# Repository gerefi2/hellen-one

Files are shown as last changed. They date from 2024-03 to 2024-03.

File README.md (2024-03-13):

# TL,DR: 

hellen-one is a toolset to produce custom PCBs by merging gerber files of known proven functional modules into trivial _frame_ PCB with mostly just the main vehicle connector.

* fork https://github.com/gerefi/hellen-example/ repo to get github actions and meta files
* make sure github actions are enabled/enable github actions on your fork
* replace xxx and yyy in ``revision.txt`` with name of your board
* create youboard.kicad_pcb from [proven modules](https://github.com/gerefi2/hellen-one/tree/master/modules) using KiCAD 6 or 7
* push into github to trigger hellen-one gerber expert and gerber merge (that's where the hellen magic happens! for instance gerber export is taken care by [export.sh](https://github.com/gerefi2/hellen-one/blob/master/kicad/bin/export.sh) script which github action would invoke _automatically_. Just watch for the yellow circle to turn into a green checkmark.)
* (sorry rotation only by factor of 90 degrees at this point)
* order your using fabrication files from 'boards' folder!

Please see how some of the open source boards are done and follow the pattern:

## Open Source Boards

* https://github.com/gerefi/alphax-4chan
* https://github.com/gerefi/uaefi
* https://github.com/gerefi/alphax-2chan
* https://github.com/gerefi/hellen154hyundai
* https://github.com/gerefi/hellen121vag
* https://github.com/gerefi/hellen88bmw
* https://github.com/gerefi2/hellen81/

This repository contains all scripts and data to create Hellen One boards for [gerefi](https://github.com/gerefi/gerefi)!

See also https://github.com/gerefi/gerefi/wiki/Hellen-One-Platform

Hellen One is a DIY PnP ECU board construction toolset.

Do you have a car with a rare or non-standard ECU connector pinout?
Do you want a custom DIY ECU but don't want to design it from scratch?

Then Hellen One is for you!

Please see Hellen One Wiki for more info:

https://github.com/gerefi2/hellen-one/wiki

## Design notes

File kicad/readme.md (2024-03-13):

# Some of the modules were designed in KiCAD

If you are designing a new ECU frame see https://github.com/gerefi2/hellen-one/tree/master/modules

doThis folder contains module _source_ files, not reusable resulting frames like [here](../modules).

See https://github.com/gerefi2/hellen-one/wiki/scripts-howto#how-to-create-a-module

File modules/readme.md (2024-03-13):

This folder contains KiCAD footprints/gerbers/PDFs which hellen-one framework would merge into your frame design.

See https://github.com/gerefi2/hellen-one/wiki for module documentation

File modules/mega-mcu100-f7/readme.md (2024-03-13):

For instance 
* [https://jlcpcb.com/partdetail/Stmicroelectronics-STM32F765VGT6/C435845](STM32F765VGT6)
* STM32F777VIT6
* STM32F767VIT6
* STM32F765VIT6

Full list see https://github.com/gerefi2/hellen-one/issues/341

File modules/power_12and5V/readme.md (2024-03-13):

See https://github.com/gerefi2/hellen-one/wiki/module-power12-and-5

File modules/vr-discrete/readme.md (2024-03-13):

See https://github.com/gerefi2/hellen-one/wiki/module-vr-discrete

[Source files](../../kicad/modules/hellen1-vr-discrete)

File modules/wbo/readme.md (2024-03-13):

[Source files](../../kicad/modules/hellen1-wbo)

## Changelog

0.4:
  - two side assembly
  - BUG: CANH/CANL traces are flipped

0.3: 
  - MOSFET through-hole option 
  - https://github.com/gerefi2/hellen-one/blob/master/modules/wbo/wbo-0.3-migration.png remove one track and refill zones
     
0.3 v2:
  - 1mm vias under MOSFET for hand soldering

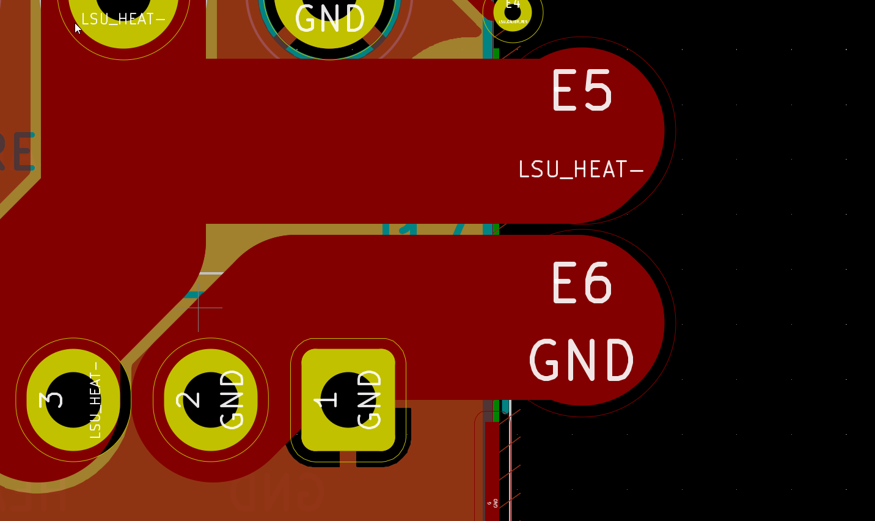
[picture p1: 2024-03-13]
modules/wbo/wbo-0.3-migration.png

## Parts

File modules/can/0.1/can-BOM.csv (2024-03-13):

Comment | Designator | Footprint | LCSC Part #
100n | C430, C431 | C0603 | C14663
PESD1CAN | D430 | SOT-23 | C343993
Hellen One : CAN Module interface | M430
120 | R430 | R0603 | C22787
TJA1051T/3/1J | U430 | SO8 | C38695

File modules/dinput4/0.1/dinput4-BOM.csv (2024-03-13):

Comment | Designator | Footprint | LCSC Part #
1n | C490, C491, C492, C493 | C0603 | C1588
Module:dinput4/0.1 | M490
680k | R490 | R0603-4 | C145776
10k | R491 | R0603-4 | C29718
74HC2G17GW | U490, U491 | SOT-363 | C94189

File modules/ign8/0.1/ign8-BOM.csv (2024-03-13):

Comment | Designator | Footprint | LCSC Part #
100n | C460, C461 | C0603 | C14663
Module:ign8/0.1 | M460
10 | R461, R462, R463, R464, R466, R467, R468, R469 | R0603 | C22859
SN74LVC4245APWR | U460 | TSSOP24 | C7859

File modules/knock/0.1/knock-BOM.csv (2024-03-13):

Comment | Designator | Footprint | LCSC Part #
100n | C470 | C0603 | C14663
3.3n | C471 | C0603 | C1613
330p | C472 | C0603 | C1664
47p | C473 | C0603 | C1671
680p | C474 | C0603 | C1630
Module:knock/0.1 | M470
470k | R470 | R0603 | C23178
100k | R471, R473 | R0603 | C25803
12k | R472 | R0603 | C22790
33k | R474 | R0603 | C4216
LMV321IDBVR | U470, U471 | SOT23-5 | C7972

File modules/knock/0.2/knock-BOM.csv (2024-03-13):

Comment | Designator | Footprint | LCSC Part #
100n | C470 | C0402 | C307331
3.3n | C471 | C0402 | C26404
330p | C472 | C0402 | C13533
47p | C473 | C0402 | C1567
680p | C474 | C0603 | C1630
Module:knock/0.2 | M470
470k | R470 | R0402 | C25790
100k | R471, R473 | R0402 | C25741
12k | R472 | R0402 | C25752
33k | R474 | R0402 | C25779
LMV321IDBVR | U470, U471 | SOT23-5 | C7972

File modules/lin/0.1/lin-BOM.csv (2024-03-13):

Comment | Designator | Footprint | LCSC Part #
100n | C440 | C0603 | C14663
B5819W | D440, D441 | SOD-123 | C8598
Hellen One : LIN Module interface | M440
1k | R440 | R0603 | C21190
TJA1021T/20/CM | U440 | SO8 | C128810

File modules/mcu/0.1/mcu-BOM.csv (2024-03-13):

Comment | Designator | Footprint | LCSC Part #
100n | C101, C105, C106, C107, C108, C109, C110, C111, C112, C113, C117, C118, C119, C120, C121, C122, C123, C124, C125, C126, C127, C128, C129, C130, C135, C139 | C0603 | C14663
4.7u | C102, C103, C104, C137, C138, C140 | C0603 | C19666
2.2u | C114, C131 | C0603 | C23630
12p | C115, C116 | C0603 | C38523
18p | C132, C136 | C0603 | C1647
B5819W | D101, D107 | SOD-123 | C8598
SRV05-4-P-T7 | D102 | SOT23-6 | C85364
LED-RED-0603 | D103 | LED-0603 | C2286
LED-GREEN-0603 | D104 | LED-0603 | C72043
LED-BLUE-0603 | D105 | LED-0603 | C72041
LED-YELLOW-0603 | D106 | LED-0603 | C72038
SDFL2012Q3R3KTF | L101 | L0805 | C51725
Module:mcu/0.1 | M101
4.7k | R101, R107, R108, R109, R110, R111, R112, R113, R115, R117, R118, R125, R126 | R0603-4 | C66697
10k | R102, R103, R105, R121, R122, R123, R127, R128 | R0603 | C25804
100 | R104, R106 | R0603 | C22775
47 | R114 | R0603 | C23182
510 | R116, R119, R120, R124 | R0603 | C23193
10k | R129, R130 | R0603-4 | C29718
0 | R131 | R0402 | C17168
AMS1117-3.3 | U101 | SOT-223 | C6186
LMV324IPWR | U102, U104, U106, U107, U108, U109 | TSSOP14 | C398929
AP2337SA-7 | U103 | SOT-23 | C150497
STM32F427IGT6 | U105 | LQFP176 | C117817
XC6206P332MR | U111 | SOT-23 | C5446
32.768 kHz | Y101 | SMD2012 | C99009
8.0 MHz | Y102 | SMD5032 | C115962

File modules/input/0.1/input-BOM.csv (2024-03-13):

Comment | Designator | Footprint | LCSC Part #
1n | C200, C202, C203, C216, C217, C218, C219 | C0603 | C1588
10n | C201, C208, C209, C210, C211 | C0603 | C57112
100n | C204, C205, C206, C207, C212, C213, C214, C215, C220, C221, C222, C223, C224, C225, C226 | C0603 | C14663
2.2u | C227, C228, C229 | C0805 | C49217
SRV05-4-P-T7 | D200, D201, D202, D203, D204, D205 | SOT23-6 | C85364
P6SMB6.8CA | D206 | SMB | C78395
Module:input/0.1 | M200
4.7k | R200, R201, R202, R203, R204, R205, R207 | R0603-4 | C1980
680k | R206, R209, R211 | R0603-4 | C145776
10k | R208, R210 | R0603-4 | C29718
510 | R212, R213, R214, R215 | R0603 | C23193
3.3k | R216 | R0603 | C22978

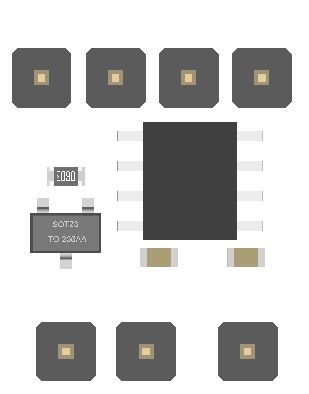
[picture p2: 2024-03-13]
tests/boards.EXAMPLE/hellen1test-a/board/misc/hellen1test-a-components.png

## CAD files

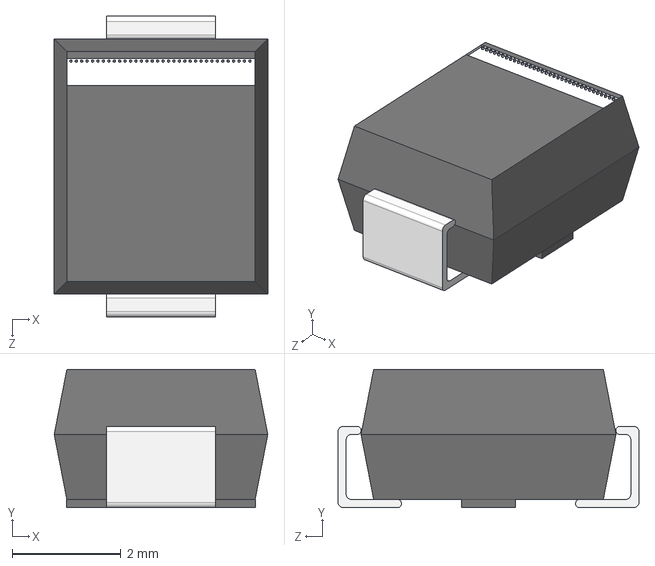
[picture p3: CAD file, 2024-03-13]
kicad/models/DO-214AA(SMB).STEP
3.94 x 2.55 x 5.55 mm

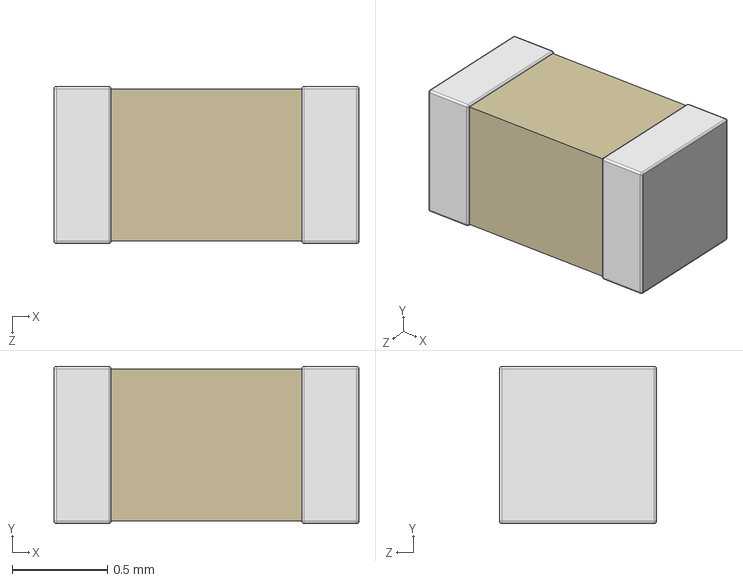
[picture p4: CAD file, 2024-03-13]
kicad/models/0603 cap.STEP
1.60 x 0.824 x 0.824 mm

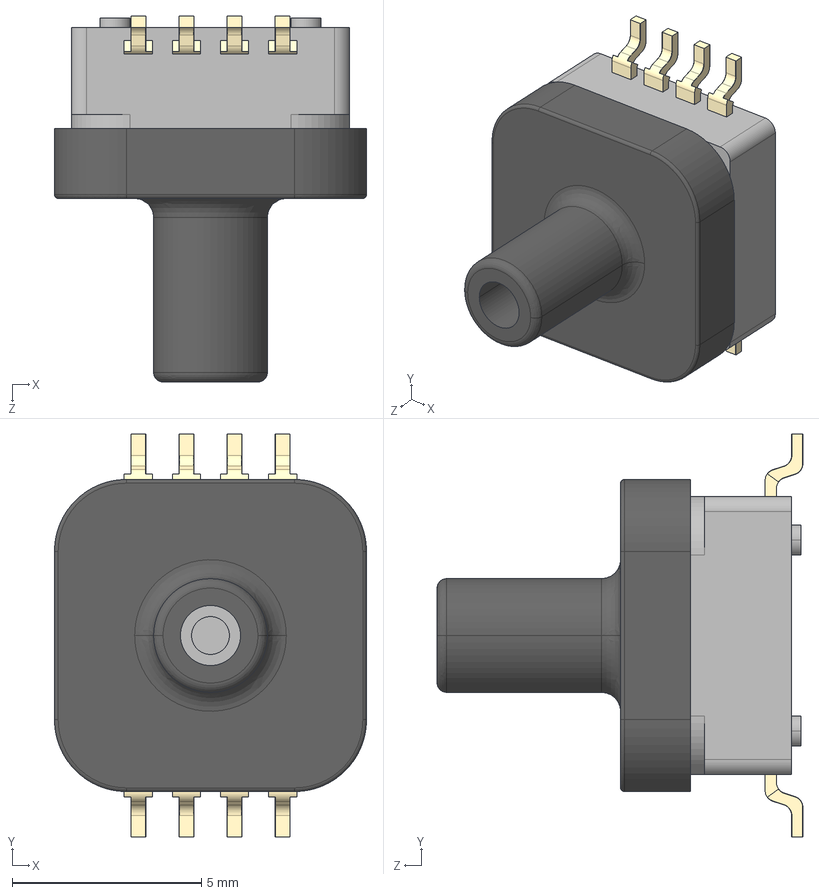
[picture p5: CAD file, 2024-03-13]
kicad/models/MPXH6400A.STEP
8.25 x 10.7 x 9.67 mm
User Library-ZlozenieMPXH6400A_Komin
User Library-ZlozenieMPXH6400A_podstawa
User Library-ZlozenieMPXH6400A_NOGA x 8

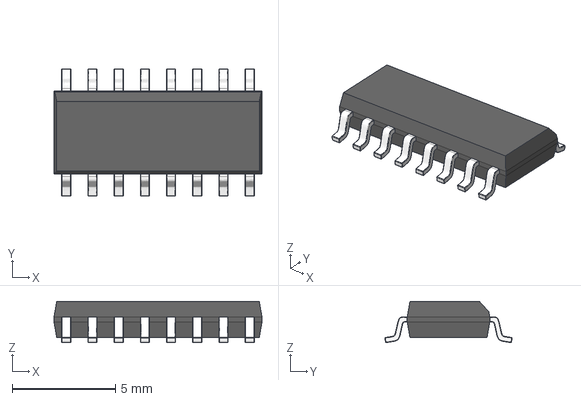
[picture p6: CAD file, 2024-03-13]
kicad/models/SOIC16 narrow.STEP
10.1 x 6.16 x 2.00 mm

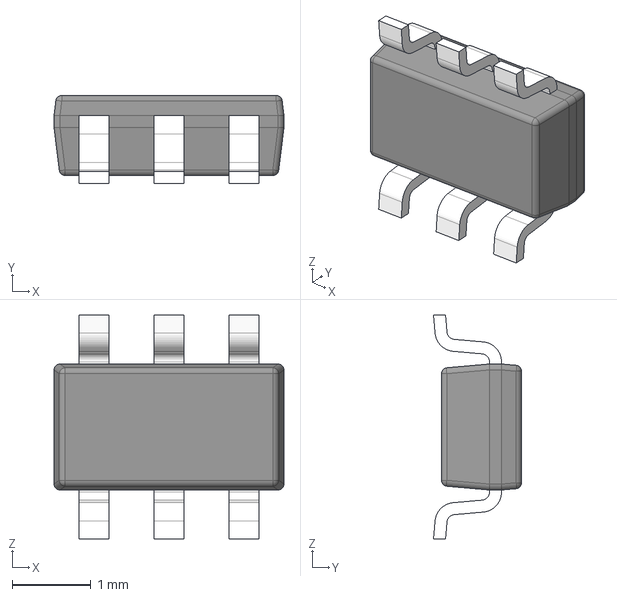
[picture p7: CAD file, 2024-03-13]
kicad/models/sot-23-6.stp
2.92 x 1.12 x 2.84 mm
BODY_MF06A
LEAD_MF06A x 6

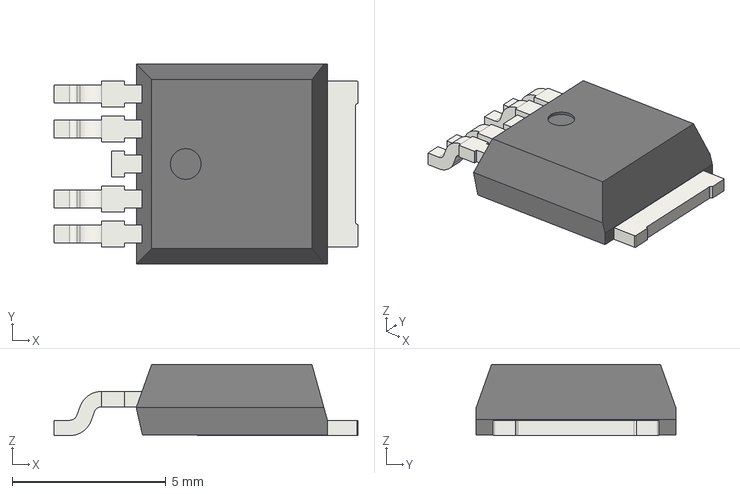
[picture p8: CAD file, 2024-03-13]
kicad/models/DPAK-5.STEP
9.90 x 6.50 x 2.32 mm

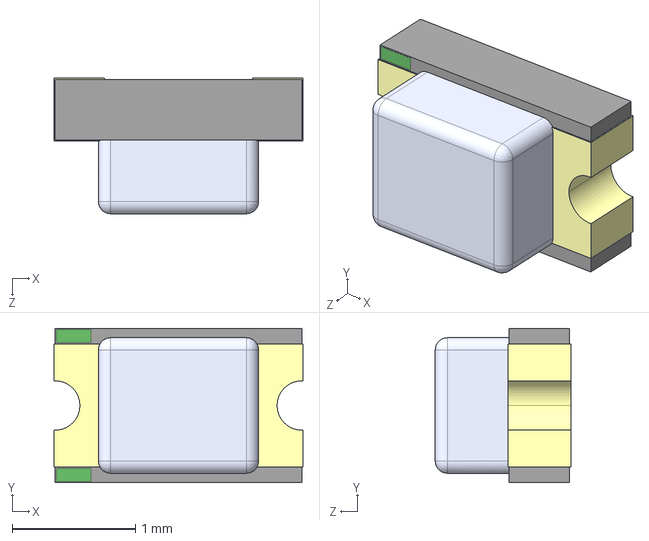
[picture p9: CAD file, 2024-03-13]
kicad/models/LED0805-YELLOW.STEP
2.02 x 1.25 x 1.10 mm

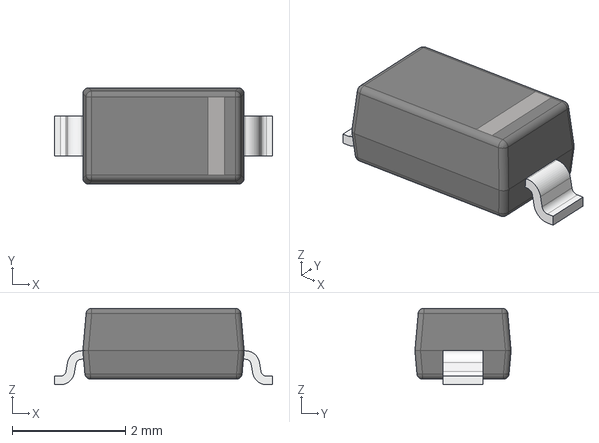
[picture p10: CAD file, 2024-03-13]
kicad/models/DO-215AD.stp
3.85 x 1.70 x 1.35 mm

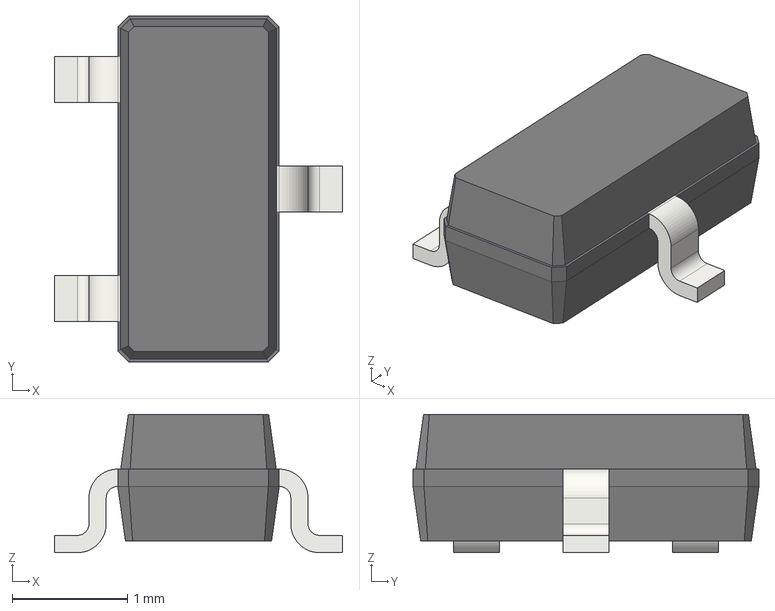
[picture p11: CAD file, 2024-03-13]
kicad/models/SOT-23.STEP
2.50 x 3.00 x 1.20 mm

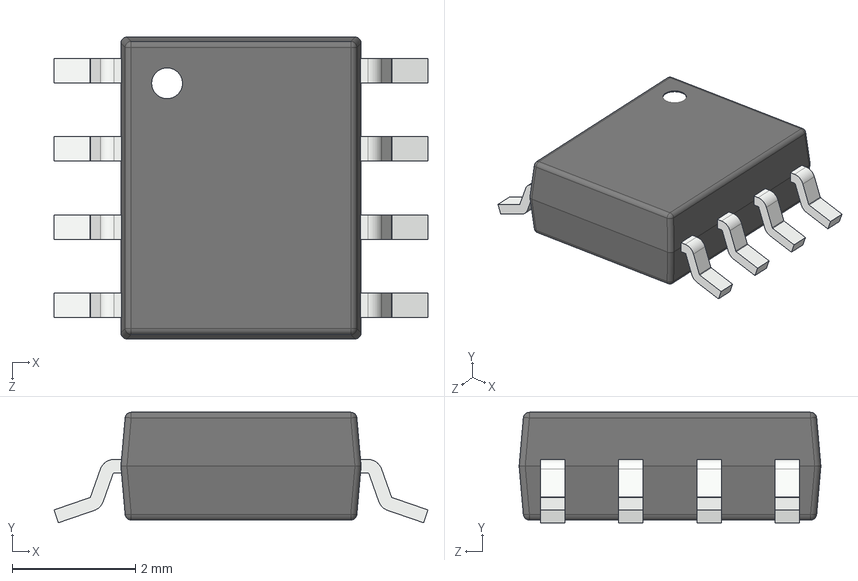
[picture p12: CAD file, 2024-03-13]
kicad/models/PG-DSO-8.STEP
6.07 x 1.79 x 4.90 mm

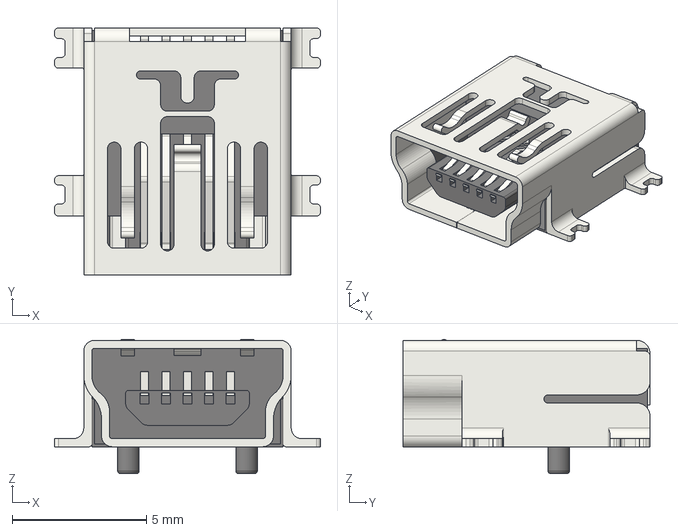
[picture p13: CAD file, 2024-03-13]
kicad/models/USB-Mini-B-Horizontal.STEP
9.90 x 9.20 x 5.00 mm

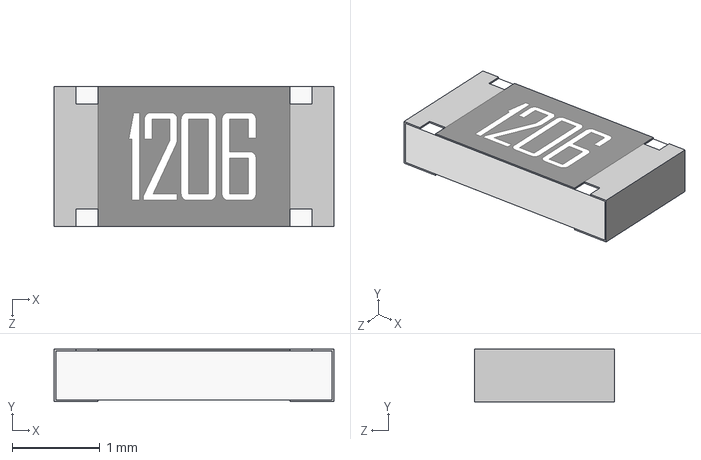
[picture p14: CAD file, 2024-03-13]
kicad/models/1206 resistor.STEP
3.20 x 0.6 x 1.60 mm

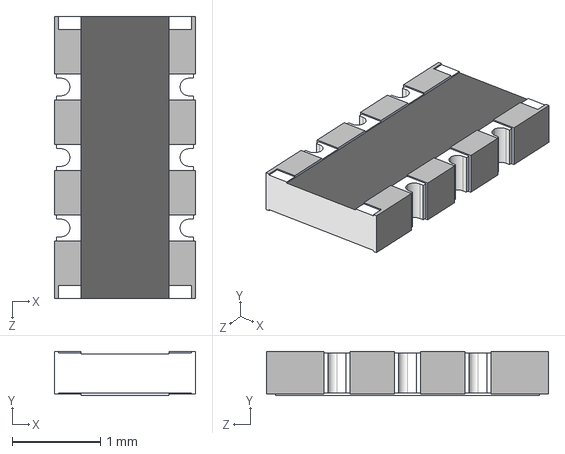
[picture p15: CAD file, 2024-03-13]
kicad/models/CAY16-F4.STEP
1.60 x 0.5 x 3.20 mm

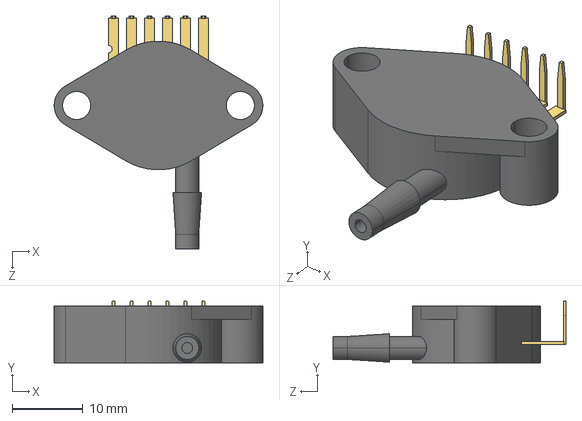
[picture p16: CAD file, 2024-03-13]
kicad/models/MPX4250AP.STEP
29.5 x 8.72 x 32.9 mm

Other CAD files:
kicad/models/SOD323F.STEP
kicad/models/SOIC08 narrow.STEP
kicad/models/USB-B-Vertical.step
kicad/models/DPAK.STEP
kicad/models/0402 resistor.STEP
kicad/models/0603 resistor.STEP
kicad/models/0805 cap.STEP
kicad/models/0805 resistor.STEP
kicad/models/LGA-12-2x2x0_9.STEP
kicad/models/PinHeader_1x06_P2.54mm_Vertical.STEP
kicad/models/PinHeader_1x08_P2.54mm_Vertical.STEP
kicad/models/PinHeader_2x05_P1.27mm_Vertical_SMD.STEP
kicad/models/PowerSO20.STEP
kicad/models/SKRKAHE020.STEP
kicad/models/SOD123F.STEP
kicad/models/SOT-223.STEP
kicad/models/SOT-363.STEP
kicad/models/TSSOP14.STEP

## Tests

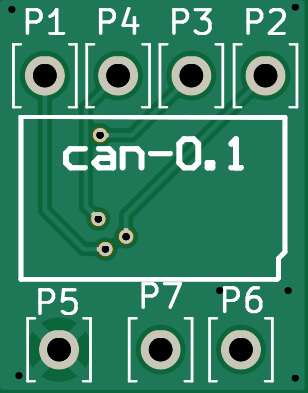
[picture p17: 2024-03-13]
tests/boards.EXAMPLE/hellen1test-a/board/misc/hellen1test-a-bottom.png

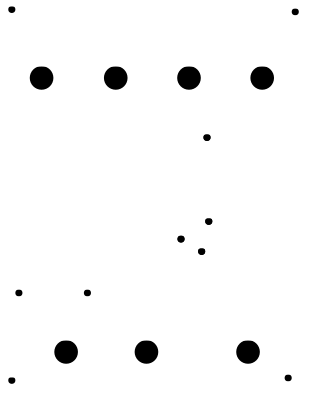
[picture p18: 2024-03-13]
tests/boards.EXAMPLE/hellen1test-a/board/misc/hellen1test-a-outline.png

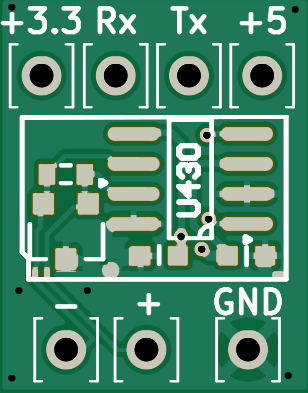
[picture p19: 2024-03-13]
tests/boards.EXAMPLE/hellen1test-a/board/misc/hellen1test-a-top.png

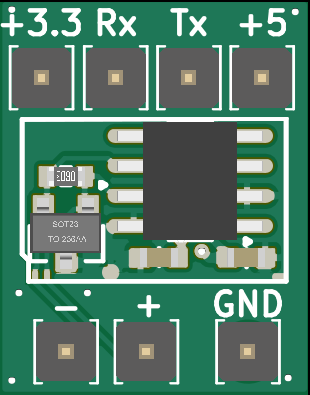
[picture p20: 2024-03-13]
tests/boards.EXAMPLE/hellen1test-a/board/hellen1test-a.png

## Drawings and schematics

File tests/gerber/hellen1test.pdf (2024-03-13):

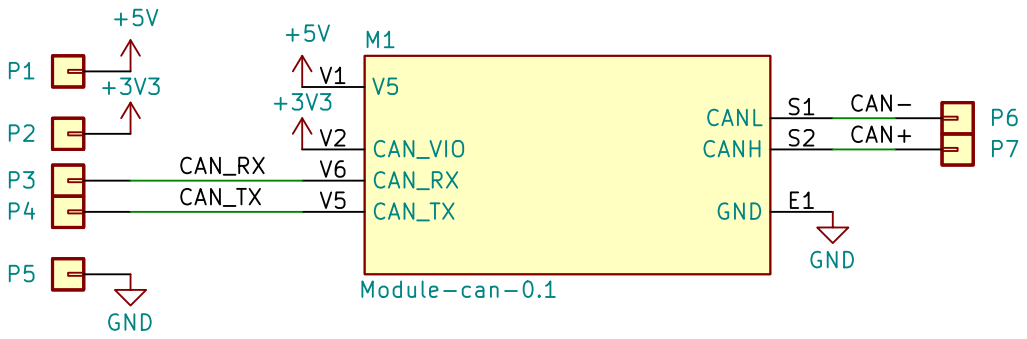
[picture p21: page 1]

File: hellen1test.kicad_sch Sheet: /
Id: 1/1 Title: Hellen-One Test Board

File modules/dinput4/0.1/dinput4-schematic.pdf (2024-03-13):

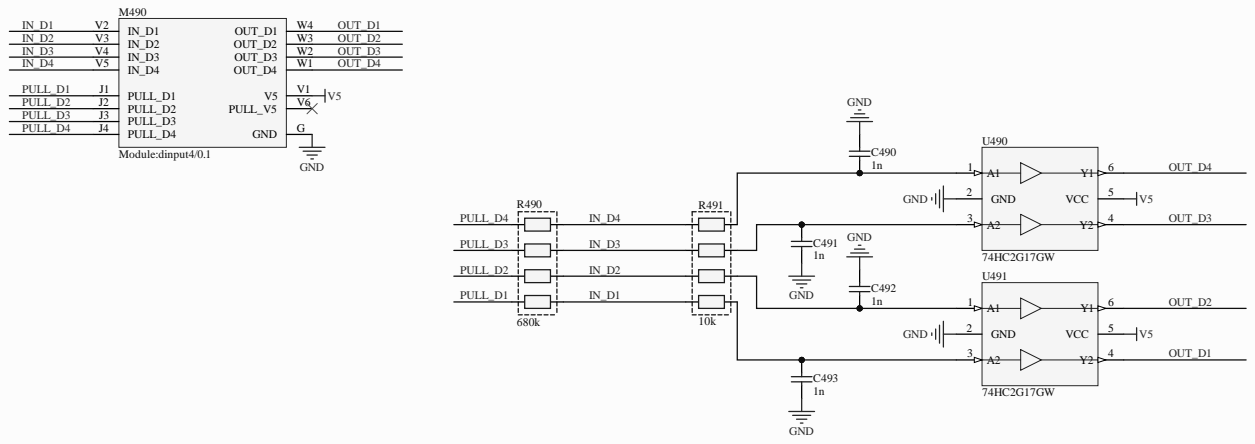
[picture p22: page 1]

Hellen-One VR andreika

rusEFI EMS https://rusefi.co
Hellen-One

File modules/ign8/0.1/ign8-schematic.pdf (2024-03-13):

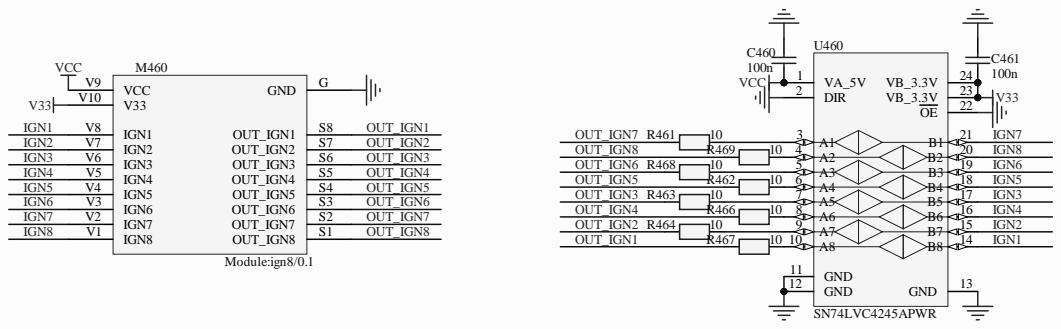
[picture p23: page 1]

rusEFI EMS https://rusefi.co
Hellen-One

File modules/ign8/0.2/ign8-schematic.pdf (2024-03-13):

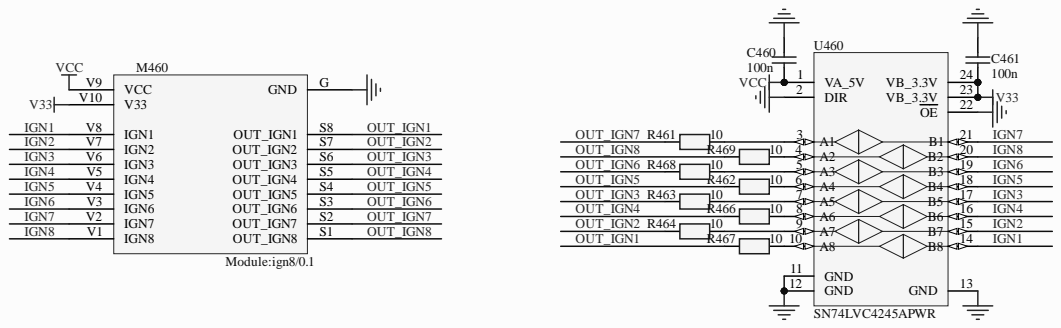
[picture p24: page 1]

rusEFI EMS https://rusefi.co
Hellen-One

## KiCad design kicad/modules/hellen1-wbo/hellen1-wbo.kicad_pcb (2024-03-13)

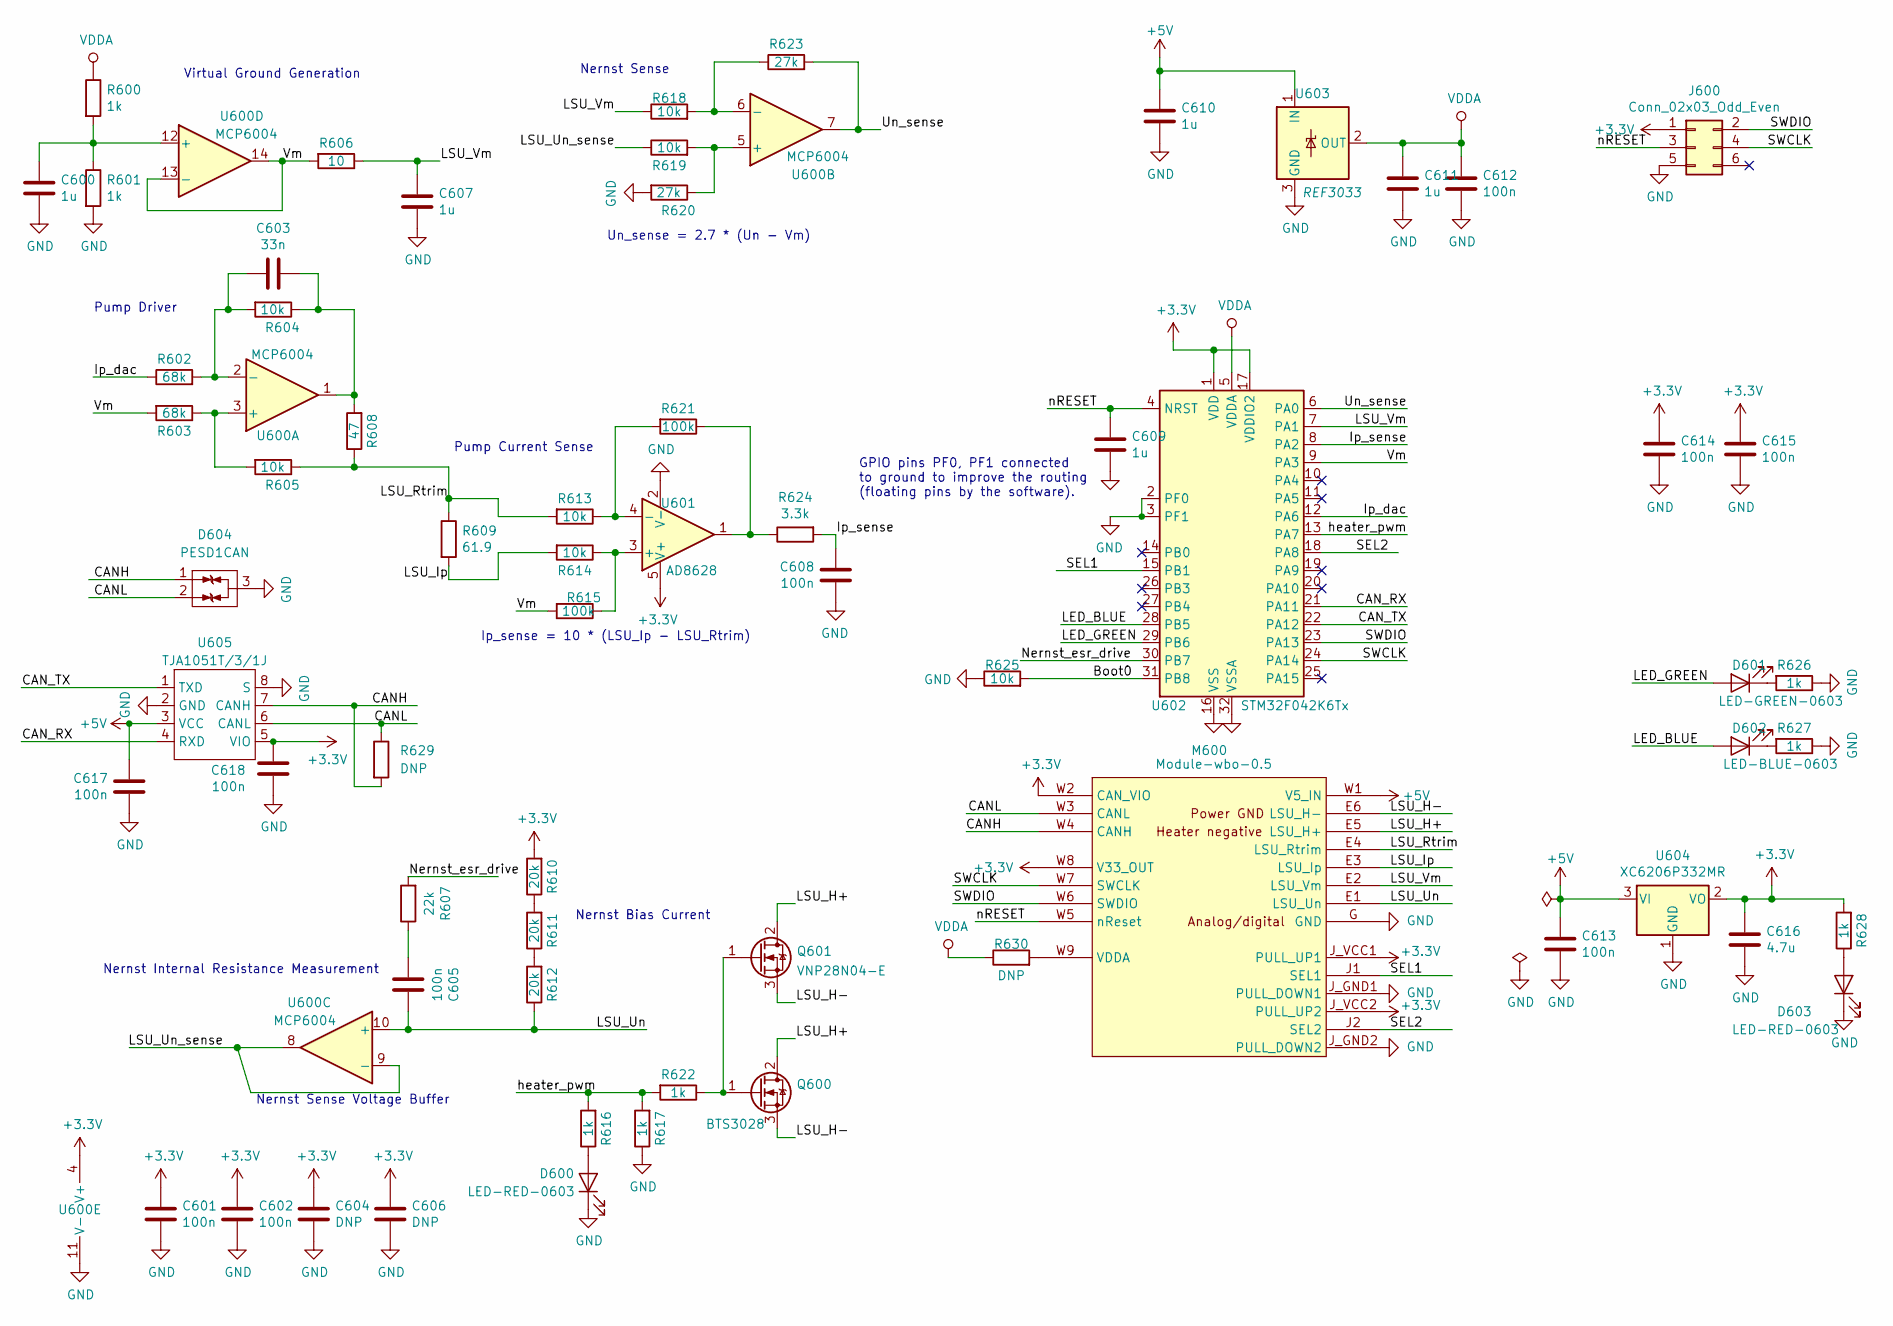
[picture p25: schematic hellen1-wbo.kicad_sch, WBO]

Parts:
C600, C607, C609, C610, C611: 1u; C_0402_1005Metric; LCSC C52923
C601, C602, C605, C608, C612, C613, C614, C615, C617, C618: 100n; C_0402_1005Metric; LCSC C1525
C603: 33n; C_0402_1005Metric; LCSC C1585
C604, C606: DNP; C_0402_1005Metric
C616: 4.7u; C_0603_1608Metric; LCSC C19666
D600, D603: LED-RED-0603; LED_0603_1608Metric; LCSC C2286
D601: LED-GREEN-0603; LED_0603_1608Metric; LCSC C72043
D602: LED-BLUE-0603; LED_0603_1608Metric; LCSC C72041
D604: PESD1CAN; SOT-23; LCSC C343993
J600: Conn_02x03_Odd_Even; Tag-Connect_TC2030-IDC-NL_2x03_P1.27mm_Vertical
M600: Module-wbo-0.5; wbo
Q600: BTS3028; TO-252-2; LCSC C112639
Q601: VNP28N04-E; TO-220-3_Vertical; LCSC C263002
R600, R601, R616, R617, R622, R626, R627, R628: 1k; R_0402_1005Metric; LCSC C11702
R602, R603: 68k; R_0402_1005Metric; LCSC C36871
R604, R605, R613, R614, R618, R619, R625: 10k; R_0402_1005Metric; LCSC C25744
R606: 10; R_0402_1005Metric; LCSC C25077
R607: 22k; R_0402_1005Metric; LCSC C25768
R608: 47; R_0402_1005Metric; LCSC C25118
R609: 61.9; R_0603_1608Metric; LCSC C23092
R610, R611, R612: 20k; R_0402_1005Metric; LCSC C25765
R615, R621: 100k; R_0402_1005Metric; LCSC C25741
R620, R623: 27k; R_0402_1005Metric; LCSC C25771
R624: 3.3k; R_0402_1005Metric; LCSC C25890
R629, R630: DNP; R_0402_1005Metric
U600: MCP6004; TSSOP-14_4.4x5mm_P0.65mm; LCSC C50282
U601: AD8628; TSOT-23-5; LCSC C29309
U602: STM32F042K6Tx; LQFP-32_7x7mm_P0.8mm; LCSC C69216
U603: REF3033; SOT-23; LCSC C36658
U604: XC6206P332MR; SOT-23; LCSC C5446
U605: TJA1051T/3/1J; SO-8_3.9x4.9mm_P1.27mm; LCSC C38695

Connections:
+3V3: C601.1, C602.1, C604.1, C606.1, C614.1, C615.1, C616.1, C618.1, J600.1, M600.J_VCC1 (PULL_UP1), M600.J_VCC2 (PULL_UP2), M600.W2 (CAN_VIO), M600.W8 (V33_OUT), R610.2, R628.2, U600.4 (V+), U601.5 (V+), U602.1 (VDD), U602.17 (VDDIO2), U604.2 (VO), U605.5 (VIO)
+5V: C610.1, C613.1, C617.1, M600.W1 (V5_IN), U603.1 (IN), U604.3 (VI), U605.3 (VCC)
/Boot0: R625.2, U602.31 (PB8)
/CANH: D604.1 (G), M600.W4 (CANH), R629.2, U605.7 (CANH)
/CANL: D604.2 (D), M600.W3 (CANL), R629.1, U605.6 (CANL)
/CAN_RX: U602.21 (PA11), U605.4 (RXD)
/CAN_TX: U602.22 (PA12), U605.1 (TXD)
/Ip_dac: R602.1, U602.12 (PA6)
/Ip_sense: C608.1, R624.2, U602.8 (PA2)
/LED_BLUE: D602.2 (A), U602.28 (PB5)
/LED_GREEN: D601.2 (A), U602.29 (PB6)
/LSU_H+: M600.E5 (LSU_H+), Q600.2 (D), Q601.2 (D)
/LSU_H-: M600.E6 (LSU_H-), Q600.3 (S), Q601.3 (S)
/LSU_Ip: M600.E3 (LSU_Ip), R609.2, R614.2
/LSU_Rtrim: M600.E4 (LSU_Rtrim), R605.1, R608.1, R609.1, R613.2
/LSU_Un: C605.1, M600.E1 (LSU_Un), R612.1, U600.10 (+)
/LSU_Un_sense: R619.1, U600.8, U600.9 (-)
/LSU_Vm: C607.1, M600.E2 (LSU_Vm), R606.1, R618.1, U602.7 (PA1)
/Nernst_esr_drive: R607.2, U602.30 (PB7)
/SEL1: M600.J1 (SEL1), U602.15 (PB1)
/SEL2: M600.J2 (SEL2), U602.18 (PA8)
/SWCLK: J600.4, M600.W7 (SWCLK), U602.24 (PA14)
/SWDIO: J600.2, M600.W6 (SWDIO), U602.23 (PA13)
/Un_sense: R623.2, U600.7, U602.6 (PA0)
/Vm: R603.2, R606.2, R615.2, U600.13 (-), U600.14, U602.9 (PA3)
/heater_pwm: R616.2, R617.2, R622.2, U602.13 (PA7)
/nRESET: C609.1, J600.3, M600.W5 (nReset), U602.4 (NRST)
GND: C600.2, C601.2, C602.2, C604.2, C606.2, C607.2, C608.2, C609.2, C610.2, C611.2, C612.2, C613.2, C614.2, C615.2, C616.2, C617.2, C618.2, D600.1 (K), D603.1 (K), D604.3 (S), J600.5, M600.G (GND), M600.J_GND1 (PULL_DOWN1), M600.J_GND2 (PULL_DOWN2), R601.2, R617.1, R620.2, R625.1, R626.1, R627.1, U600.11 (V-), U601.2 (V-), U602.2 (PF0), U602.3 (PF1), U602.16 (VSS), U602.32 (VSSA), U603.3 (GND), U604.1 (GND), U605.2 (GND), U605.8 (S)
unnamed: C600.1, R600.2, R601.1, U600.12 (+)
unnamed: C603.1, R604.1, R608.2, U600.1
unnamed: C603.2, R602.2, R604.2, U600.2 (-)
unnamed: C605.2, R607.1
unnamed: D600.2 (A), R616.1
unnamed: D601.1 (K), R626.2
unnamed: D602.1 (K), R627.2
unnamed: D603.2 (A), R628.1
unnamed: M600.W9 (VDDA), R630.2
unnamed: Q600.1 (G), Q601.1 (G), R622.1
unnamed: R603.1, R605.2, U600.3 (+)
unnamed: R610.1, R611.2
unnamed: R611.1, R612.2
unnamed: R613.1, R621.2, U601.4 (-)
unnamed: R614.1, R615.1, U601.3 (+)
unnamed: R618.2, R623.1, U600.6 (-)
unnamed: R619.2, R620.1, U600.5 (+)
unnamed: R621.1, R624.1, U601.1
VDDA: C611.1, C612.1, R600.1, R630.1, U602.5 (VDDA), U603.2 (OUT)

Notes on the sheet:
Nernst Sense
Pump Driver
Virtual Ground Generation
Nernst Internal Resistance Measurement
Nernst Bias Current
Nernst Sense Voltage Buffer
Un_sense = 2.7 * (Un - Vm)
Pump Current Sense
Ip_sense = 10 * (LSU_Ip - LSU_Rtrim)
GPIO pins PF0, PF1 connected to ground to improve the routing (floating pins by the software).

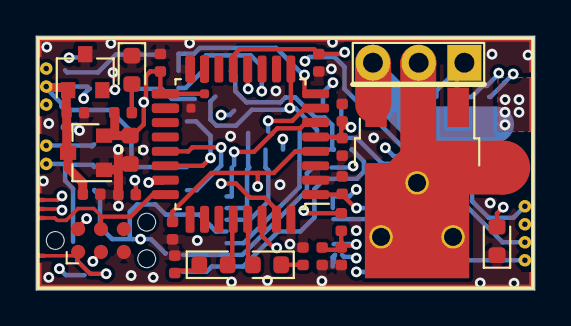
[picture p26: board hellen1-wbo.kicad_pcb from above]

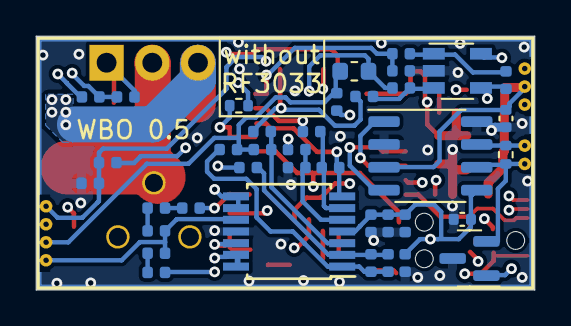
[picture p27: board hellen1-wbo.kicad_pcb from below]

Board: 4 copper layers, 27.7 x 14.1 mm, 65 parts (38 on the bottom side), 47 nets.

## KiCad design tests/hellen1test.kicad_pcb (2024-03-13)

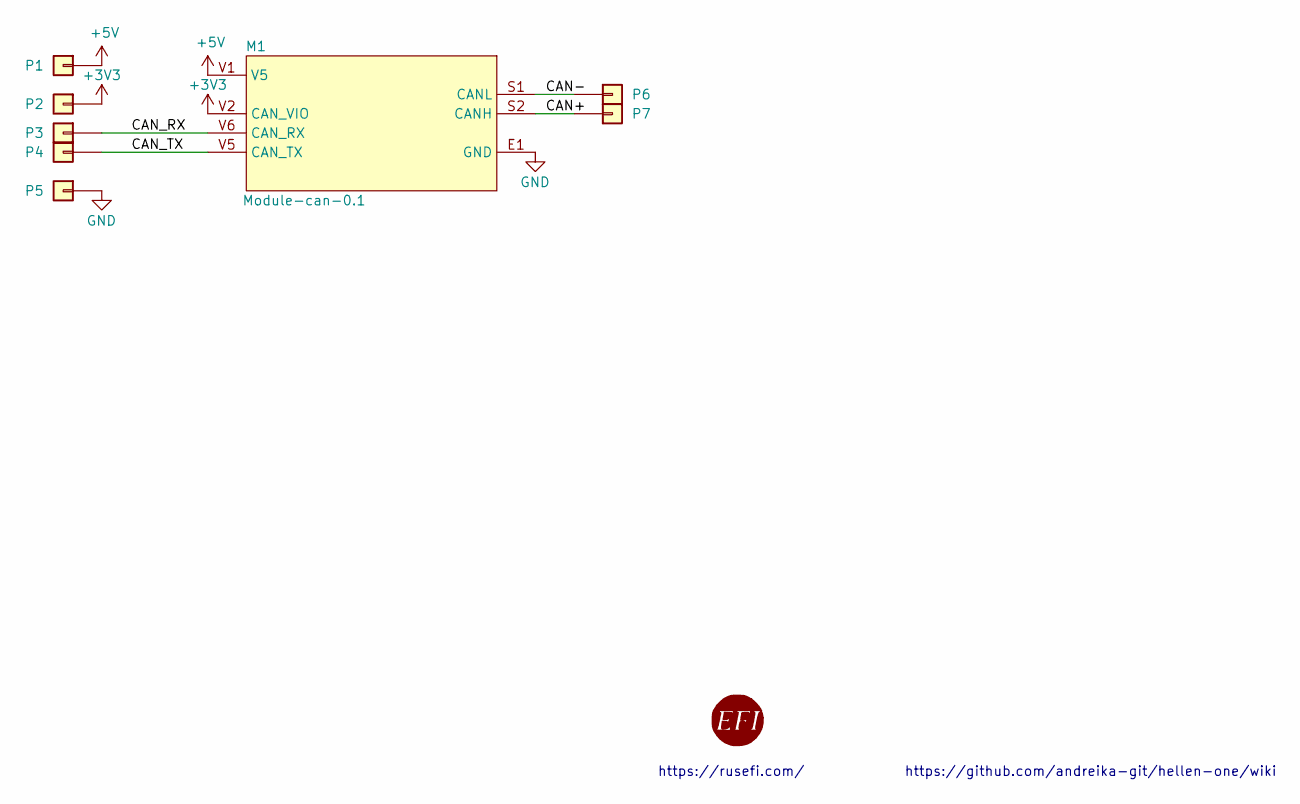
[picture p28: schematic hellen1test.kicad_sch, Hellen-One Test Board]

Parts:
M1: Module-can-0.1; can
P1, P2, P3, P4, P5, P6, P7: Pad; PAD-TH

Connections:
+3V3: M1.V2 (CAN_VIO), P2.1
+5V: M1.V1 (V5), P1.1
/CAN+: M1.S2 (CANH), P7.1
/CAN-: M1.S1 (CANL), P6.1
/CAN_RX: M1.V6 (CAN_RX), P3.1
/CAN_TX: M1.V5 (CAN_TX), P4.1
GND: M1.E1 (GND), P5.1

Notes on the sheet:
https://rusefi.com/
https://github.com/andreika-git/hellen-one/wiki

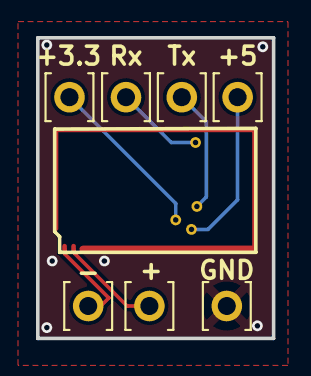
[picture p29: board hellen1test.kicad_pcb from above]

Board: 2 copper layers, 13.1 x 16.7 mm, 8 parts (0 on the bottom side), 7 nets.

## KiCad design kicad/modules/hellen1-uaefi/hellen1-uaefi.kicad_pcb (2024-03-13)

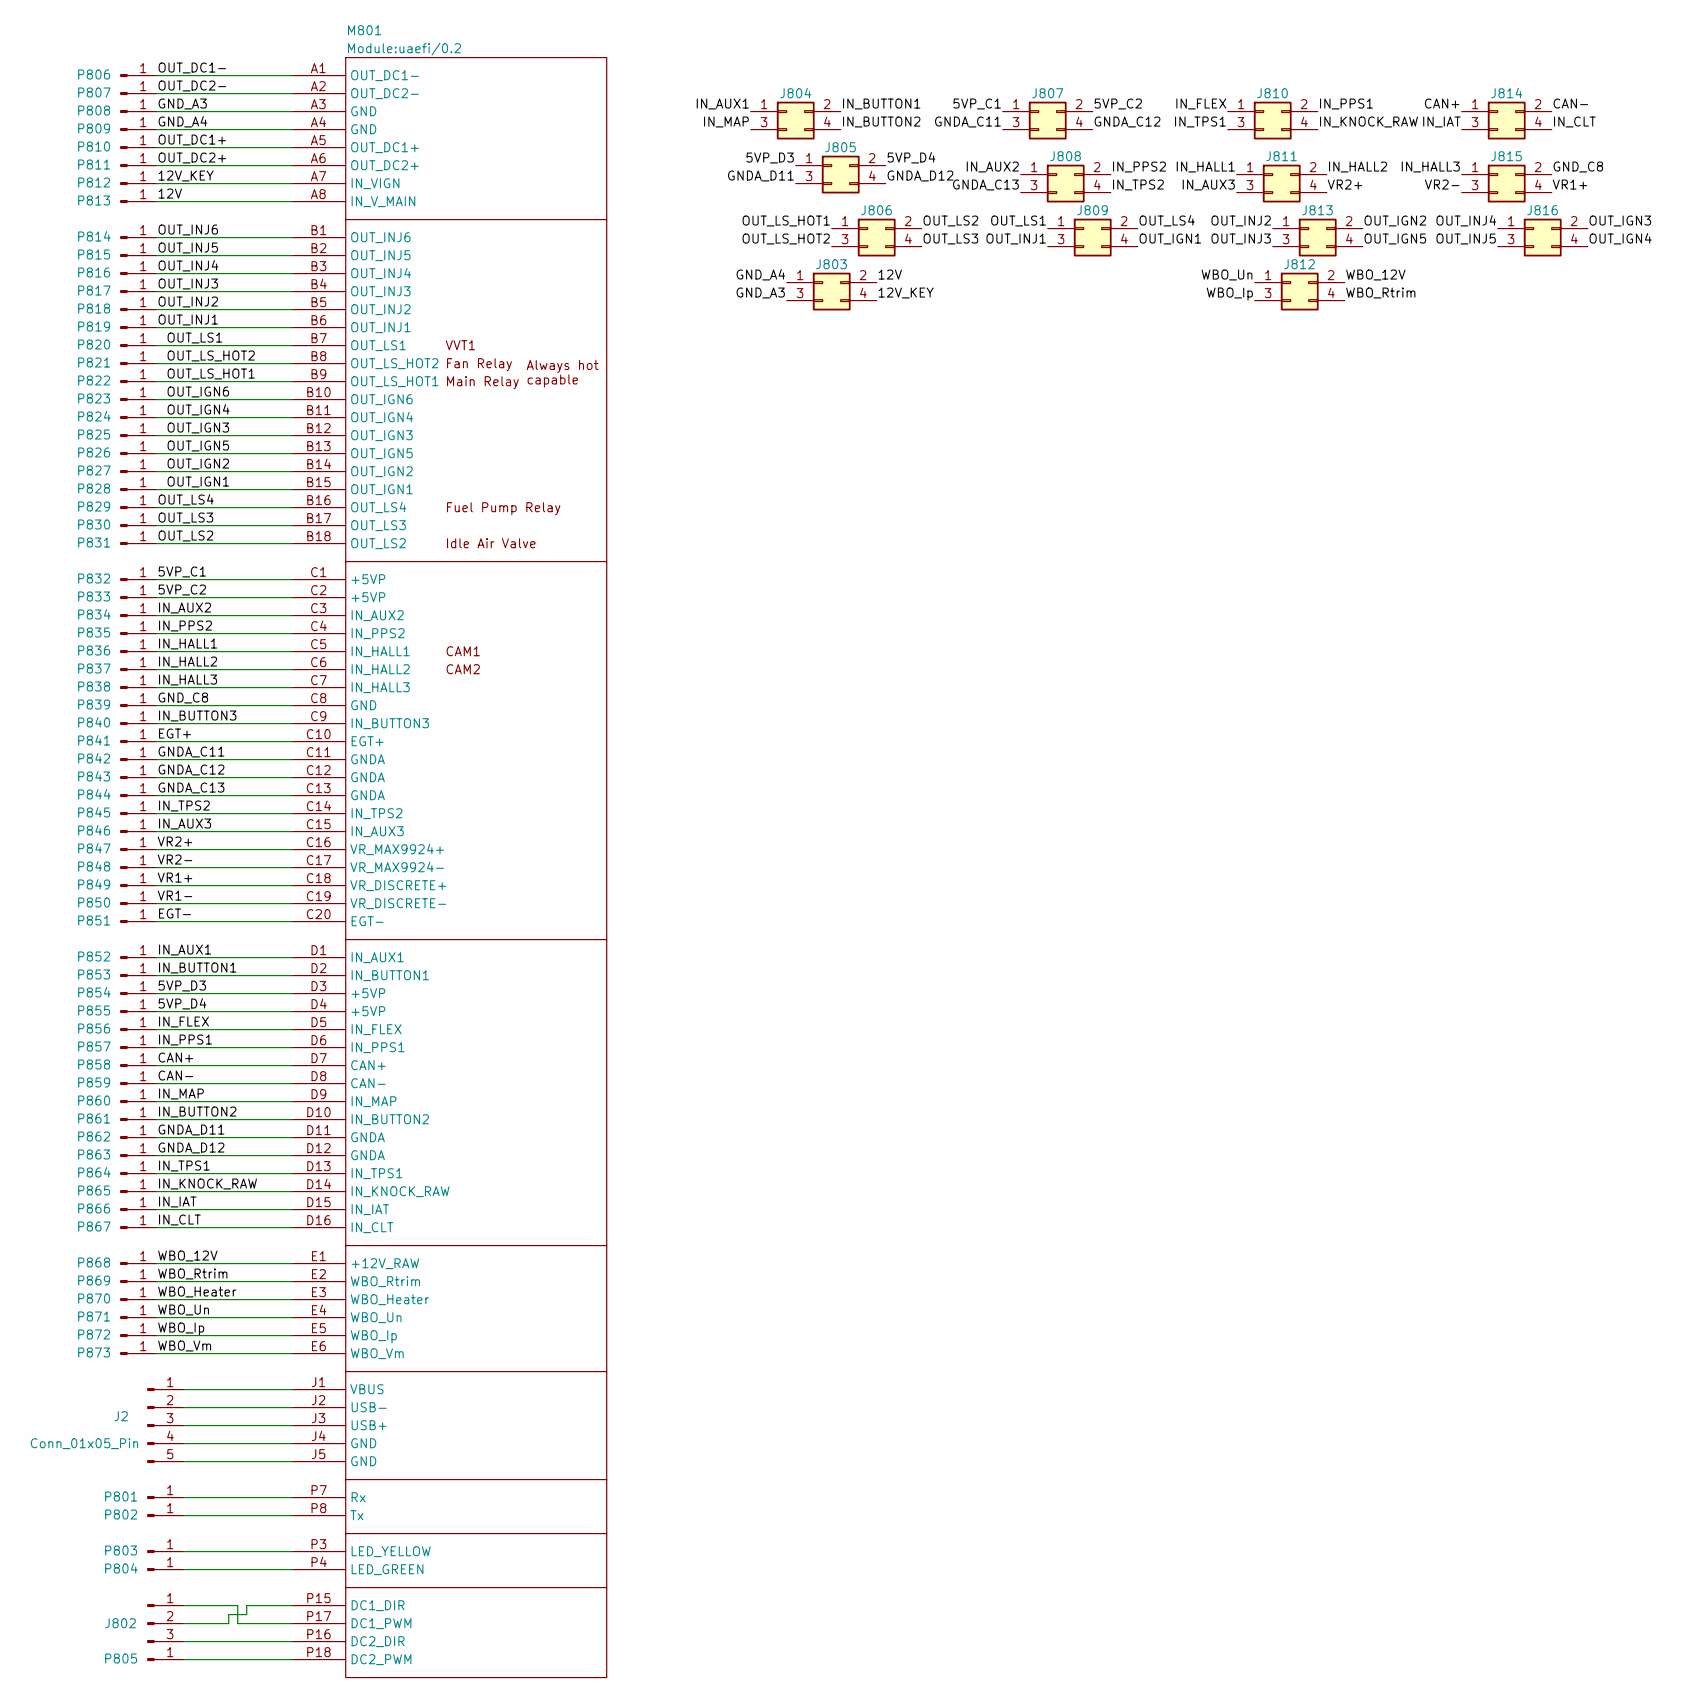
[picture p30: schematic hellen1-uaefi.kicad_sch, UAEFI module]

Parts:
J2: Conn_01x05_Pin; Molex_SPOX_5267-05A_1x05_P2.50mm_Vertical; LCSC C492404
J802: Conn_01x03_Pin; 1x3_2.54; LCSC C49257
J803, J804, J805, J806, J807, J808, J809, J810, J811, J812, J813, J814, J815, J816: Conn_02x02_Odd_Even; 2x2_2.54; LCSC C492419
M801: Module:uaefi/0.2; uaefi
P801, P802, P803, P804, P805: Conn_01x01_Pin; 1x1; LCSC C81276
P806, P807, P808, P809, P810, P811, P812, P813, P814, P815, P816, P817, P818, P819, P820, P821, P822, P823, P824, P825, P826, P827, P828, P829, P830, P831, P832, P833, P834, P835, P836, P837, P838, P839, P840, P841, P842, P843, P844, P845, P846, P847, P848, P849, P850, P851, P852, P853, P854, P855, P856, P857, P858, P859, P860, P861, P862, P863, P864, P865, P866, P867, P868, P869, P870, P871, P872, P873: RT-01T-1.0B; LCSC C265321

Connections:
/5VP_C1: J807.1, M801.C1 (+5VP), P832.1
/5VP_C2: J807.2, M801.C2 (+5VP), P833.1
/5VP_D3: J805.1, M801.D3 (+5VP), P854.1
/5VP_D4: J805.2, M801.D4 (+5VP), P855.1
/12V: J803.2, M801.A8 (IN_V_MAIN), P813.1
/12V_KEY: J803.4, M801.A7 (IN_VIGN), P812.1
/CAN+: J814.1, M801.D7 (CAN+), P858.1
/CAN-: J814.2, M801.D8 (CAN-), P859.1
/EGT+: M801.C10 (EGT+), P841.1
/EGT-: M801.C20 (EGT-), P851.1
/GNDA_C11: J807.3, M801.C11 (GNDA), P842.1
/GNDA_C12: J807.4, M801.C12 (GNDA), P843.1
/GNDA_C13: J808.3, M801.C13 (GNDA), P844.1
/GNDA_D11: J805.3, M801.D11 (GNDA), P862.1
/GNDA_D12: J805.4, M801.D12 (GNDA), P863.1
/GND_A3: J803.3, M801.A3 (GND), P808.1
/GND_A4: J803.1, M801.A4 (GND), P809.1
/GND_C8: J815.2, M801.C8 (GND), P839.1
/IN_AUX1: J804.1, M801.D1 (IN_AUX1), P852.1
/IN_AUX2: J808.1, M801.C3 (IN_AUX2), P834.1
/IN_AUX3: J811.3, M801.C15 (IN_AUX3), P846.1
/IN_BUTTON1: J804.2, M801.D2 (IN_BUTTON1), P853.1
/IN_BUTTON2: J804.4, M801.D10 (IN_BUTTON2), P861.1
/IN_BUTTON3: M801.C9 (IN_BUTTON3), P840.1
/IN_CLT: J814.4, M801.D16 (IN_CLT), P867.1
/IN_FLEX: J810.1, M801.D5 (IN_FLEX), P856.1
/IN_HALL1: J811.1, M801.C5 (IN_HALL1), P836.1
/IN_HALL2: J811.2, M801.C6 (IN_HALL2), P837.1
/IN_HALL3: J815.1, M801.C7 (IN_HALL3), P838.1
/IN_IAT: J814.3, M801.D15 (IN_IAT), P866.1
/IN_KNOCK_RAW: J810.4, M801.D14 (IN_KNOCK_RAW), P865.1
/IN_MAP: J804.3, M801.D9 (IN_MAP), P860.1
/IN_PPS1: J810.2, M801.D6 (IN_PPS1), P857.1
/IN_PPS2: J808.2, M801.C4 (IN_PPS2), P835.1
/IN_TPS1: J810.3, M801.D13 (IN_TPS1), P864.1
/IN_TPS2: J808.4, M801.C14 (IN_TPS2), P845.1
/OUT_DC1+: M801.A5 (OUT_DC1+), P810.1
/OUT_DC1-: M801.A1 (OUT_DC1-), P806.1
/OUT_DC2+: M801.A6 (OUT_DC2+), P811.1
/OUT_DC2-: M801.A2 (OUT_DC2-), P807.1
/OUT_IGN1: J809.4, M801.B15 (OUT_IGN1), P828.1
/OUT_IGN2: J813.2, M801.B14 (OUT_IGN2), P827.1
/OUT_IGN3: J816.2, M801.B12 (OUT_IGN3), P825.1
/OUT_IGN4: J816.4, M801.B11 (OUT_IGN4), P824.1
/OUT_IGN5: J813.4, M801.B13 (OUT_IGN5), P826.1
/OUT_IGN6: M801.B10 (OUT_IGN6), P823.1
/OUT_INJ1: J809.3, M801.B6 (OUT_INJ1), P819.1
/OUT_INJ2: J813.1, M801.B5 (OUT_INJ2), P818.1
/OUT_INJ3: J813.3, M801.B4 (OUT_INJ3), P817.1
/OUT_INJ4: J816.1, M801.B3 (OUT_INJ4), P816.1
/OUT_INJ5: J816.3, M801.B2 (OUT_INJ5), P815.1
/OUT_INJ6: M801.B1 (OUT_INJ6), P814.1
/OUT_LS1: J809.1, M801.B7 (OUT_LS1), P820.1
/OUT_LS2: J806.2, M801.B18 (OUT_LS2), P831.1
/OUT_LS3: J806.4, M801.B17 (OUT_LS3), P830.1
/OUT_LS4: J809.2, M801.B16 (OUT_LS4), P829.1
/OUT_LS_HOT1: J806.1, M801.B9 (OUT_LS_WEAK1), P822.1
/OUT_LS_HOT2: J806.3, M801.B8 (OUT_LS_WEAK2), P821.1
/VR1+: J815.4, M801.C18 (VR_DISCRETE+), P849.1
/VR1-: M801.C19 (VR_DISCRETE-), P850.1
/VR2+: J811.4, M801.C16 (VR_MAX9924+), P847.1
/VR2-: J815.3, M801.C17 (VR_MAX9924-), P848.1
/WBO_12V: J812.2, M801.E1 (+12V_RAW), P868.1
/WBO_Heater: M801.E3 (WBO_Heater), P870.1
/WBO_Ip: J812.3, M801.E5 (WBO_Ip), P872.1
/WBO_Rtrim: J812.4, M801.E2 (WBO_Rtrim), P869.1
/WBO_Un: J812.1, M801.E4 (WBO_Un), P871.1
/WBO_Vm: M801.E6 (WBO_Vm), P873.1
unnamed 68: M801.J1 (VBUS); also elsewhere on the board
unnamed 69: M801.J2 (USB-); also elsewhere on the board
unnamed 70: M801.J3 (USB+); also elsewhere on the board
unnamed 71: M801.J4 (GND); also elsewhere on the board
unnamed 72: M801.J5 (GND); also elsewhere on the board
unnamed: J802.1, M801.P17 (DC1_PWM)
unnamed: J802.2, M801.P15 (DC1_DIR)
unnamed: J802.3, M801.P16 (DC2_DIR)
unnamed: M801.P18 (DC2_PWM), P805.1
unnamed: M801.P4 (LED_GREEN), P804.1
unnamed: M801.P3 (LED_YELLOW), P803.1
unnamed: M801.P7 (Rx), P801.1
unnamed: M801.P8 (Tx), P802.1

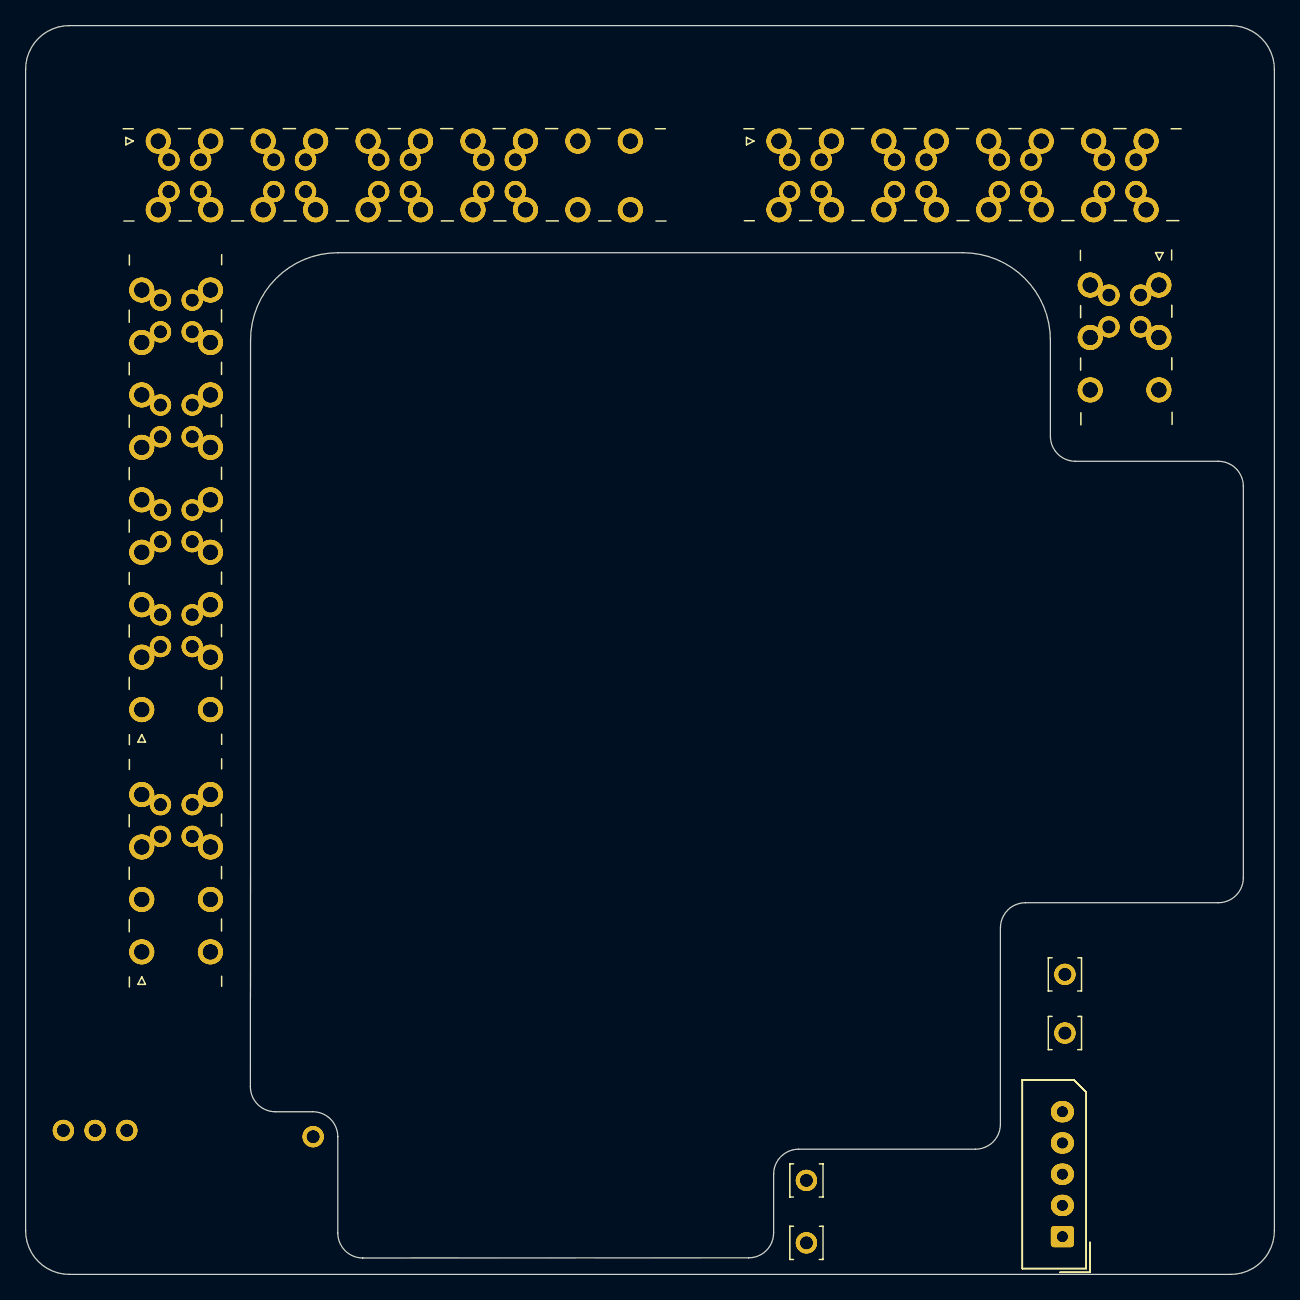
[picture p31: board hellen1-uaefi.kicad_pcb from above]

Board: 4 copper layers, 100.0 x 100.0 mm, 90 parts (0 on the bottom side), 81 nets.

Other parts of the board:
J801: Conn_01x05_Pin; Molex_SPOX_5267-05A_1x05_P2.50mm_Vertical

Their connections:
unnamed 68: J801.1; also elsewhere on the board
unnamed 69: J801.2; also elsewhere on the board
unnamed 70: J801.3; also elsewhere on the board
unnamed 71: J801.4; also elsewhere on the board
unnamed 72: J801.5; also elsewhere on the board

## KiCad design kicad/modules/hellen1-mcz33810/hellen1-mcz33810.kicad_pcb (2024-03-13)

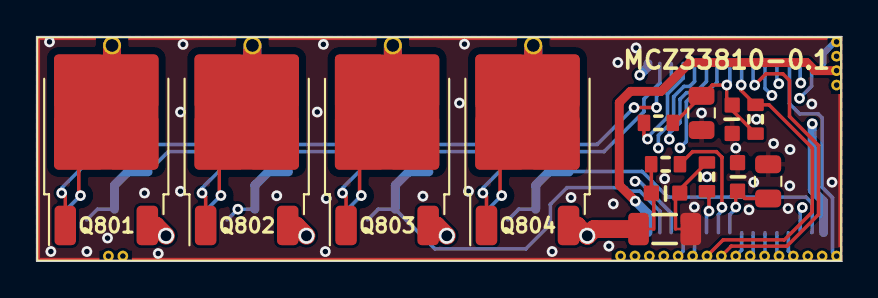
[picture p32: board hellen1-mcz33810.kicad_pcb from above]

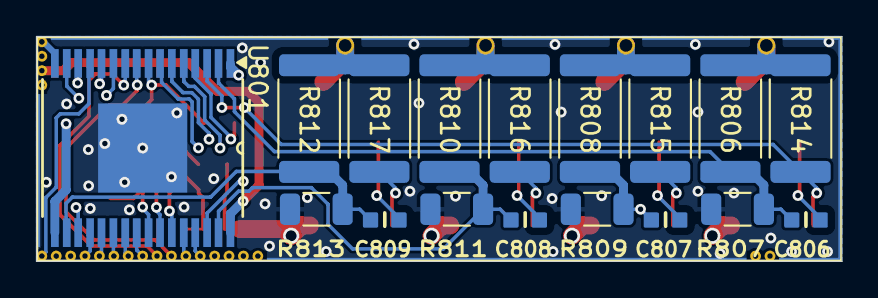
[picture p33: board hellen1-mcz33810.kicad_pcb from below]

Board: 4 copper layers, 44.8 x 12.5 mm, 32 parts (17 on the bottom side), 40 nets.

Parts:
C801, C804: 100n; C0603
C802, C805: 10u; C_0805_2012Metric
C803: 100p; C0603
C806, C807, C808, C809: 10p; C0603
M801: Module-mcz33810-0.1; mcz33810
Q801, Q802, Q803, Q804: ISL9V3040D3S; TO-252-2
R801, R802: 10k; R0603
R803, R804: 100; R0603
R805: 0.02; Shunt_1206
R806, R808, R810, R812: 36k; R_2512_6332Metric
R807, R809, R811, R813: 4.02k; R_1206_3216Metric
R814, R815, R816, R817: DNP; R_2512_6332Metric
U801: MCZ33810EK; Mcz33810

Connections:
+3V3: C801.1, C802.2, M801.S18 (3V3_IN), R801.2, R802.2, U801.8 (VDD)
+12V: C804.1, C805.2, M801.S17 (12V_IN), U801.25 (VPWR)
/IGN1: M801.S8 (IGN1), U801.24 (GIN0)
/IGN2: M801.S7 (IGN2), U801.23 (GIN1)
/IGN3: M801.S6 (IGN3), U801.22 (GIN2)
/IGN4: M801.S5 (IGN4), U801.21 (GIN3)
/INJ1: M801.S9 (INJ1), U801.10 (DIN0)
/INJ2: M801.S3 (INJ2), U801.11 (DIN1)
/INJ3: M801.S2 (INJ3), U801.12 (DIN2)
/INJ4: M801.S1 (INJ4), U801.13 (DIN3)
/MAXI: M801.S12 (MAXI), U801.29 (MAXI)
/MISO: M801.S13 (MISO), U801.7 (SO)
/MOSI: M801.S14 (MOSI), U801.6 (SI)
/NOMI: M801.S11 (NOMI), U801.28 (NOMI)
/OUT_IGN1: C806.1, M801.N1 (OUT_IGN1), Q801.2 (C), R806.1, R814.1
/OUT_IGN2: C807.1, M801.N2 (OUT_IGN2), Q802.2 (C), R808.1, R815.1
/OUT_IGN3: C808.1, M801.N3 (OUT_IGN3), Q803.2 (C), R810.1, R816.1
/OUT_IGN4: C809.1, M801.N4 (OUT_IGN4), Q804.2 (C), R812.1, R817.1
/OUT_INJ1: M801.E3 (OUT_INJ1), U801.1 (OUT0)
/OUT_INJ2: M801.E4 (OUT_INJ2), U801.16 (OUT1)
/OUT_INJ3: M801.E2 (OUT_INJ3), U801.32 (OUT2)
/OUT_INJ4: M801.E1 (OUT_INJ4), U801.17 (OUT3)
/SCLK: M801.S15 (SCLK), U801.5 (SCLK)
/~CS: M801.S16 (~CS), R802.1, U801.4 (~CS)
/~OUTEN: M801.S10 (~OUTEN), R801.1, U801.9 (~OUTEN)
/~SPKDUR: M801.S4 (~SPKDUR), U801.20 (~SPKDUR)
GND: C801.2, C802.1, C804.2, C805.1, M801.G (GND), R805.4, R807.2, R809.2, R811.2, R813.2, U801.33 (GND)
unnamed: C803.1, R803.2, R805.2
unnamed: C803.2, R804.2, R805.3
unnamed: Q801.3 (E), Q802.3 (E), Q803.3 (E), Q804.3 (E), R805.1
unnamed: Q801.1 (G), R814.2, U801.3 (GD0)
unnamed: Q802.1 (G), R815.2, U801.14 (GD1)
unnamed: Q803.1 (G), R816.2, U801.30 (GD2)
unnamed: Q804.1 (G), R817.2, U801.19 (GD3)
unnamed: C806.2, R806.2, R807.1, U801.2 (FB0)
unnamed: C807.2, R808.2, R809.1, U801.15 (FB1)
unnamed: C808.2, R810.2, R811.1, U801.31 (FB2)
unnamed: C809.2, R812.2, R813.1, U801.18 (FB3)
unnamed: R804.1, U801.27 (RSN)
unnamed: R803.1, U801.26 (RSP)

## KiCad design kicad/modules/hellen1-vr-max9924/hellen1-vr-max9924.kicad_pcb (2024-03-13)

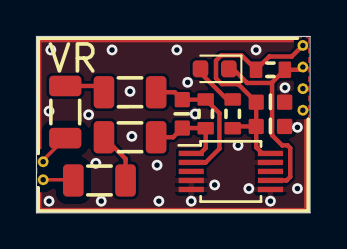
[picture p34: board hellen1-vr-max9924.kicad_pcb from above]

Board: 4 copper layers, 15.2 x 9.8 mm, 13 parts (0 on the bottom side), 10 nets.

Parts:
C771: 1n; C0603
C772: 100n; C0603
C773: 22u; C0603
D771: LED-GREEN-0603; LED_0603_1608Metric
M771: Module-vr-max9924-0.1; vr-max9924
R771, R772, R773, R774: 4.7k; R1206
R775: DNP; R0603
R776, R777: 10k; R0603
U771: MAX9924UAUB+; MSOP-10_3x3mm_P0.5mm

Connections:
+5V: C772.2, C773.2, M771.E4 (V5_IN), R776.2, R777.2, U771.10 (VCC)
GND: C772.1, C773.1, M771.G (GND), U771.4 (BIAS), U771.5 (GND), U771.6 (ZERO_EN), U771.9 (INT_THRS)
unnamed: D771.2 (A), R777.1
unnamed: R771.1, R773.2
unnamed: R772.1, R774.2
unnamed: C771.2, R773.1, R775.2, U771.1 (IN+)
unnamed: C771.1, R774.1, R775.1, U771.2 (IN-)
VR+: M771.W2 (VR+), R771.2
VR-: M771.W1 (VR-), R772.2
output: D771.1 (K), M771.E3 (OUT), R776.1, U771.7 (COUT)

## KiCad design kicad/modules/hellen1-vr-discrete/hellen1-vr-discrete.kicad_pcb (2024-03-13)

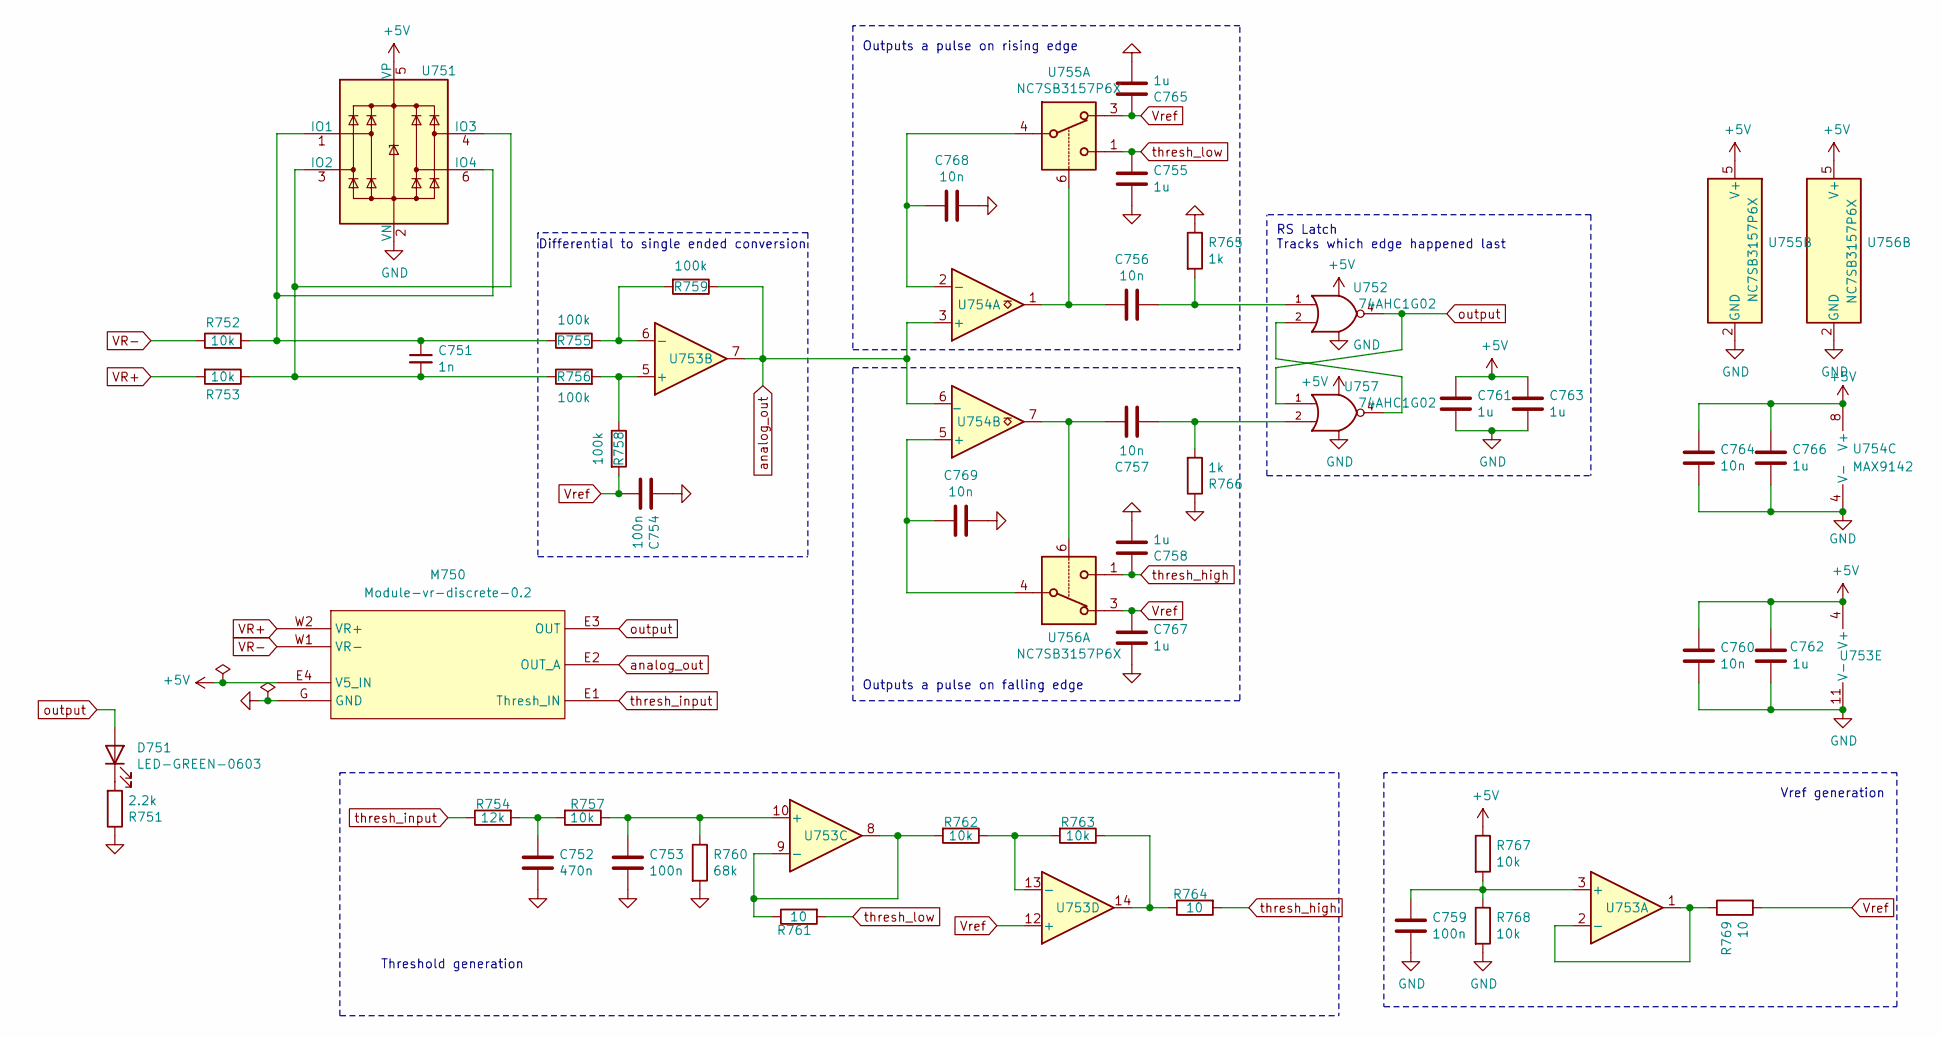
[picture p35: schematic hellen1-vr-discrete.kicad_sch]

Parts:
C751: 1n; C_0402_1005Metric; LCSC C1523
C752: 470n; C_0402_1005Metric; LCSC C47339
C753, C754, C759: 100n; C_0402_1005Metric; LCSC C1525
C755, C758, C761, C762, C763, C765, C766, C767: 1u; C_0402_1005Metric; LCSC C52923
C756, C757, C760, C764, C768, C769: 10n; C_0402_1005Metric; LCSC C15195
D751: LED-GREEN-0603; LED_0603_1608Metric; LCSC C72043
M750: Module-vr-discrete-0.2; vr-discrete
R751: 2.2k; R_0402_1005Metric; LCSC C25879
R752, R753: 10k; R_0805_2012Metric; LCSC C17414
R754: 12k; R_0402_1005Metric; LCSC C25752
R755, R756, R758, R759: 100k; R_0402_1005Metric; LCSC C25741
R757, R762, R763, R767, R768: 10k; R_0402_1005Metric; LCSC C25744
R760: 68k; R_0402_1005Metric; LCSC C36871
R761, R764, R769: 10; R_0402_1005Metric; LCSC C25077
R765, R766: 1k; R_0402_1005Metric; LCSC C11702
U751: SRV05-4-P-T7; SOT-23-6; LCSC C85364
U752, U757: 74AHC1G02; SOT-23-5; LCSC C7463
U753: MCP6004; TSSOP-14_4.4x5mm_P0.65mm; LCSC C50282
U754: MAX9142; SOIC-8_3.9x4.9mm_P1.27mm; LCSC C18567
U755, U756: NC7SB3157P6X; SOT-363_SC-70-6; LCSC C87403

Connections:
+5V: C760.1, C761.1, C762.1, C763.1, C764.1, C766.1, M750.E4 (V5_IN), R767.1, U751.5 (VP), U752.5 (VCC), U753.4 (V+), U754.8 (V+), U755.5 (V+), U756.5 (V+), U757.5 (VCC)
GND: C752.2, C753.2, C754.1, C755.2, C758.2, C759.2, C760.2, C761.2, C762.2, C763.2, C764.2, C765.2, C766.2, C767.2, C768.1, C769.1, M750.G (GND), R751.1, R760.2, R765.1, R766.1, R768.2, U751.2 (VN), U752.3 (GND), U753.11 (V-), U754.4 (V-), U755.2 (GND), U756.2 (GND), U757.3 (GND)
unnamed: C751.1, R752.2, R755.2, U751.1 (IO1), U751.6 (IO4)
unnamed: C751.2, R753.1, R756.1, U751.3 (IO2), U751.4 (IO3)
unnamed: C752.1, R754.2, R757.2
unnamed: C753.1, R757.1, R760.1, U753.10 (+)
unnamed: C756.1, R765.2, U752.1
unnamed: C756.2, U754.1, U755.6
unnamed: C757.1, R766.2, U757.2
unnamed: C757.2, U754.7, U756.6
unnamed: C759.1, R767.2, R768.1, U753.3 (+)
unnamed: D751.1 (K), R751.2
unnamed: R755.1, R759.2, U753.6 (-)
unnamed: R756.2, R758.1, U753.5 (+)
unnamed: R761.1, R762.2, U753.8, U753.9 (-)
unnamed: R762.1, R763.2, U753.13 (-)
unnamed: R763.1, R764.1, U753.14
unnamed: R769.1, U753.1, U753.2 (-)
unnamed: U752.2, U757.4
unnamed: C768.2, U754.2 (-), U755.4
unnamed: C769.2, U754.5 (+), U756.4
VR+: M750.W2 (VR+), R753.2
VR-: M750.W1 (VR-), R752.1
Vref: C754.2, C765.1, C767.1, R758.2, R769.2, U753.12 (+), U755.3, U756.3
analog_out: M750.E2 (OUT_A), R759.1, U753.7, U754.3 (+), U754.6 (_)
output: D751.2 (A), M750.E3 (OUT), U752.4, U757.1
thresh_high: C758.1, R764.2, U756.1
thresh_input: M750.E1 (Thresh_IN), R754.1
thresh_low: C755.1, R761.2, U755.1

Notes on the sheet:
RS Latch Tracks which edge happened last
Vref generation
Outputs a pulse on falling edge
Threshold generation
Outputs a pulse on rising edge
Differential to single ended conversion

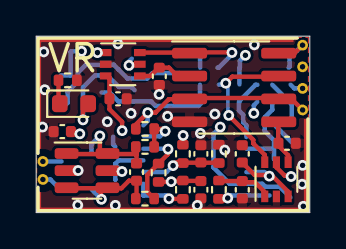
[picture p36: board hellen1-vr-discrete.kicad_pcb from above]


Board: 4 copper layers, 15.2 x 9.8 mm, 47 parts (23 on the bottom side), 29 nets.

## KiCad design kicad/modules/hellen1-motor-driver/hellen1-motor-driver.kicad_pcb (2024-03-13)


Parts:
C821, C822, C823, C824, C825, C826, C827, C828, C829, C830: 10u; C0805; LCSC C440198
C831: 100n; C0603; LCSC C14663
C832, C833: 10n; C0603; LCSC C57112
M821: Module-motor-driver-0.1; motor-driver
R137: 10k; R0603; LCSC C25804
R822: 4.7k; R0603; LCSC C23162
U821: TLE9201SG; Infineon_PG-DSO-12-11; LCSC C112633

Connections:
+3V3: M821.W5 (3V3_IN), R822.2, U821.2 (VSO); also elsewhere on the board
+12V: C821.2, C822.2, C823.2, C824.2, C825.2, C826.2, C827.2, C828.2, C829.2, C830.2, C831.2, M821.N2 (12V_IN), M821.S1 (12V_IN), U821.4 (VS)
/DIR: M821.W4 (DIR), U821.1 (DIR)
/DIS: M821.W1 (DIS), R822.1, U821.11 (DIS)
/MISO: M821.W6 (MISO), U821.3 (SO)
/MOSI: M821.N1 (MOSI), U821.8 (SI)
/OUT+: C833.2, M821.S3 (OUT+), U821.7 (OUT2)
/OUT-: C832.2, M821.S2 (OUT-), U821.5 (OUT1)
/PWM: M821.W2 (PWM), U821.12 (PWM)
/SCLK: M821.W3 (SCLK), U821.10 (SCK)
/~CS: M821.W7 (~CS), U821.9 (CSN); also elsewhere on the board
GND: C821.1, C822.1, C823.1, C824.1, C825.1, C826.1, C827.1, C828.1, C829.1, C830.1, C831.1, C832.1, C833.1, M821.G (GND), U821.6 (GND), U821.13 (GND)



Board: 4 copper layers, 13.8 x 10.0 mm, 17 parts (15 on the bottom side), 12 nets.

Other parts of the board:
R821: 10k; R0603

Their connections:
+3V3: R821.2; also elsewhere on the board
/~CS: R821.1; also elsewhere on the board

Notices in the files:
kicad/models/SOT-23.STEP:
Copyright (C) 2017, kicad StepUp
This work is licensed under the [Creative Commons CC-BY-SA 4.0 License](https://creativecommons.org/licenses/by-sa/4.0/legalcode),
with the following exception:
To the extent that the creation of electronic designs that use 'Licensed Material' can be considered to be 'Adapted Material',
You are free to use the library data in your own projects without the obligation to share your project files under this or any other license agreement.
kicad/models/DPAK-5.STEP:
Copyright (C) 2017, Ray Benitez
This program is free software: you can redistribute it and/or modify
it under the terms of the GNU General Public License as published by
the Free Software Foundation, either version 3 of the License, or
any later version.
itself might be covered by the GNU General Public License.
